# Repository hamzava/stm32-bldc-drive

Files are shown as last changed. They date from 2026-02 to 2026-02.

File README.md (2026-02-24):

# ⚡ Sensorless 3-Phase BLDC Motor Driver  
### Using STM32F411RE + IR2110 Gate Drivers + IRF3205

> 📌 **Recommended Reading:**  
> Please refer to `/Docs/BLDC Project Report.pdf` first for a detailed explanation of the architecture, technical challenges encountered, and lessons learned during development.  
> This repository documents a prototype exploration and does not represent a finalized, fully validated motor drive system.

◆ This project represents an exploration into low-level complementary PWM control, high-side bootstrap driving, and discrete 3-phase inverter design using STM32 advanced timers.

---

## ◆ Project Overview

🟥 This project is a  3-phase BLDC motor driver prototype built using:

 - **STM32F411RE** (Advanced Timer – Complementary PWM)
 - **IR2110 High/Low Side Gate Drivers**
 - IRF3205 N-Channel MOSFET Half-Bridges
 - Bootstrap High-Side Supply Topology

🟥 The objective was to implement manual commutation for a sensorless BLDC motor using complementary PWM outputs from the MCU’s advanced timer (TIM1), with register-level control and control the motor using it's BEMF.

This prototype focused on:

✔ BLDC Motor Control Algorithm
✔ Complementary PWM generation  
✔ Gate driver bootstrap behavior  
✔ Register-level commutation control  
✔ Hardware–firmware synchronization  

---
## ◆ Repository Structure
/Hardware
- ├── KiCad_Project
- ├── Gerbers
- ├── Schematics_PDF
- ├── PCB_Images

/Firmware

/Videos

/Docs
- ├── Datasheets
- ├── Resources_Used > ***All the files used to learn about technologies involved in this project***
- ├── BLDC Project Report.pdf

---

## ◆ Status

Prototype exploration complete.  
Further revision planned with improved instrumentation and driver selection.

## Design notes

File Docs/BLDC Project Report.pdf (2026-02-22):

1. System architecture overview

The architecture of the sensor less control drive was based on 3 main components. MCU, IC driver and MOSFET Half Bridges. The idea was to produce PWM using the MCU advanced timer which came with complementary output. This PWM would be used by the IC driver to produce signal for the gate of the MOSFET. We planned to have 3 Half Bridges, 1 for each Phase hence 3 IC drivers. MOSFETs were carefully chosen by considering their critical parameters, in our case for example, Rds(on), Id, Vgs(th) and Qg.

Ideally, we wanted an IC where we would send a high PWM signal to the input, and IC must output 2 complementary signals. In addition to this, an ideal IC would have been which gave us 3 I/O, one for each phase, in one IC rather than using 3 different ICs. FAN73893 was a good match. But it wasn’t available locally, making it unfeasible financially. IR2110 was a not the ideal choice. STM32F411RE was a good choice because it came with PWM. It also had ADC – DAC which we could have used for monitoring speed, speed regulation & position with DMA by using the motor’s BEMF.

2. Lack of Oscilloscope and Resulting limitations

The lack of an Oscilloscope significantly limited the validation of critical parameters for this system such as dead-time, complementary switching and bootstrap charging behaviour. This resulted in a series of after effects. This meant that we can’t visualise the waveforms which we required. We can’t gauge them being precise. Also, with DMM, the PWM is averaged but as we didn’t have an oscilloscope so subsequently, we couldn’t see if the driver was giving us the required output or was there a shoot through.

3. Manual Commutation Attempt

Initially, I wrote the code manually where I had switch cases. A function would then loop for each switch case. The limitation was that, I had to reset the relevant bits in the register with each commutation. This sort of worked but it wasn’t as smooth as expected. The likely cause was that the bit manipulation was not synchronized with the PWM. This didn’t give us a clean transition. So, I think this was an issue to be noted here which prevented me to create smoothness.

4. Discovery of COMG event & shadow registers

COMG event is an atomic event. This means that we get what we want with the least delay as the configurations are effectively transferred from the preload registers to active registers without any interruption whenever there is an update event. It works with storing values in the preload register first and then firing it into the active register when an update event occurs. But, in my opinion, it requires a higher precision of timer configuration.

5. Full timer reset + pull-down attempts

During experimentation, TIM1 CH1 pins to 5V pins on the development board. Henceforth, it wasn’t possible to continue with the project as STM32F411RE has only 3 PWM channels with complementary outputs and one of them was blown up. For TIM1 CH1 being short, we did first check, if the GPIO, AFR, MODER are set up correctly in the software or not. After that, I went through the timer bits over and over again. We set the GPIO pin to analog, but it still showed a short, it showed near zero resistance on the DMM continuity, which suggested the pin was internally short. But, we still tried to reset the timer using RCC register. Lastly, I did also try pulling it down with a resistor but apparently it didn’t work. Not conclusively, but most likely it was an internal ESD which was blown up.

6. Complementary PWM behaviour inconsistencies.

A lot of these inconsistencies stayed unresolved due to lack of an Oscilloscope. One of the most dangerous observations one can have in such a system, both outputs of the same PWM channel being high at the same time. This is the root cause of a shoot through. Furthermore, sometimes for 50% duty cycle of 3.3V signal, the main channel would should 1.6V on DMM, but the complementary channel would show 2.8V. Two issues exist here. First that the DMM suggested that both channels are high at almost the same time although this couldn’t be conclusively verified due to the lack of oscilloscope. But in software, we did hold a commutation step for enough time which let us retrieve the readings from each channel.

The second is that the complementary channel is not following the set duty cycle. For such cases, we tried manipulating registers precisely with bits such as OCxREF, OSSR, OISx, CCPC, CCUS etc as the PWM outputs are the product of some of these btis. Ideally, the channel should be disabled by CCxNE but many times we still observed an output, despite manipulating bits mentioned earlier, it didn’t change. This was one of the main cases we observed. Rest were pretty similar like a channel won’t show an output when it is supposed to or vice versa. The values wouldn’t match the duty cycle. With Point 2, I would observe switching values as per the commutation sequence but sometimes inconsistencies mentioned above occurred. After COMG implementation, we didn’t get much to observe as the TIM1 CH1 was shorted to 5V on the development board.

7. Bootstrap circuit issues

A common issue I came across with the bootstrap was that the Vs was reflected to HO pin as it is. Ideally it should be Vho=Vs+Vbs. The most likely cause was the Vdd of the driver. I isolated one half bridge and replicated the circuit. It worked as I wanted it and then I replicated it back. One of the most confusing thing was that the bootstrap capacitor was charging but it didn’t discharge. It only discharged, after my DMM probes were across it. This also shows a symptom of the IC driver not working as intended hence we get a reflection of Vs at the HO pin.

8. Importance of Flyback diode and Pull Down Registers

Upon research, there was still more room for additional protection like flyback protection and pull-down resistor at the gate of the MOSFETs. Flyback Protection would protect the MOSFETs from an inductive kickback from the motor. The pull-down resistors at the gate make sure that the gate has a defined state preventing any operation due to possible driver latch-up or any other leakages.

9. Final technical lessons

A better research on component selection and the system architecture could have been done. Projects which involve any sort of medium/high speed switching must only be done if you have an oscilloscope. Instrumentation is critical for such projects. Early access to an oscilloscope would have helped us debug the system much earlier and quicker. A thorough mental and software simulation is always needed before designing hardware. The constraints must be given appropriate time for discussion before the hardware is designed.

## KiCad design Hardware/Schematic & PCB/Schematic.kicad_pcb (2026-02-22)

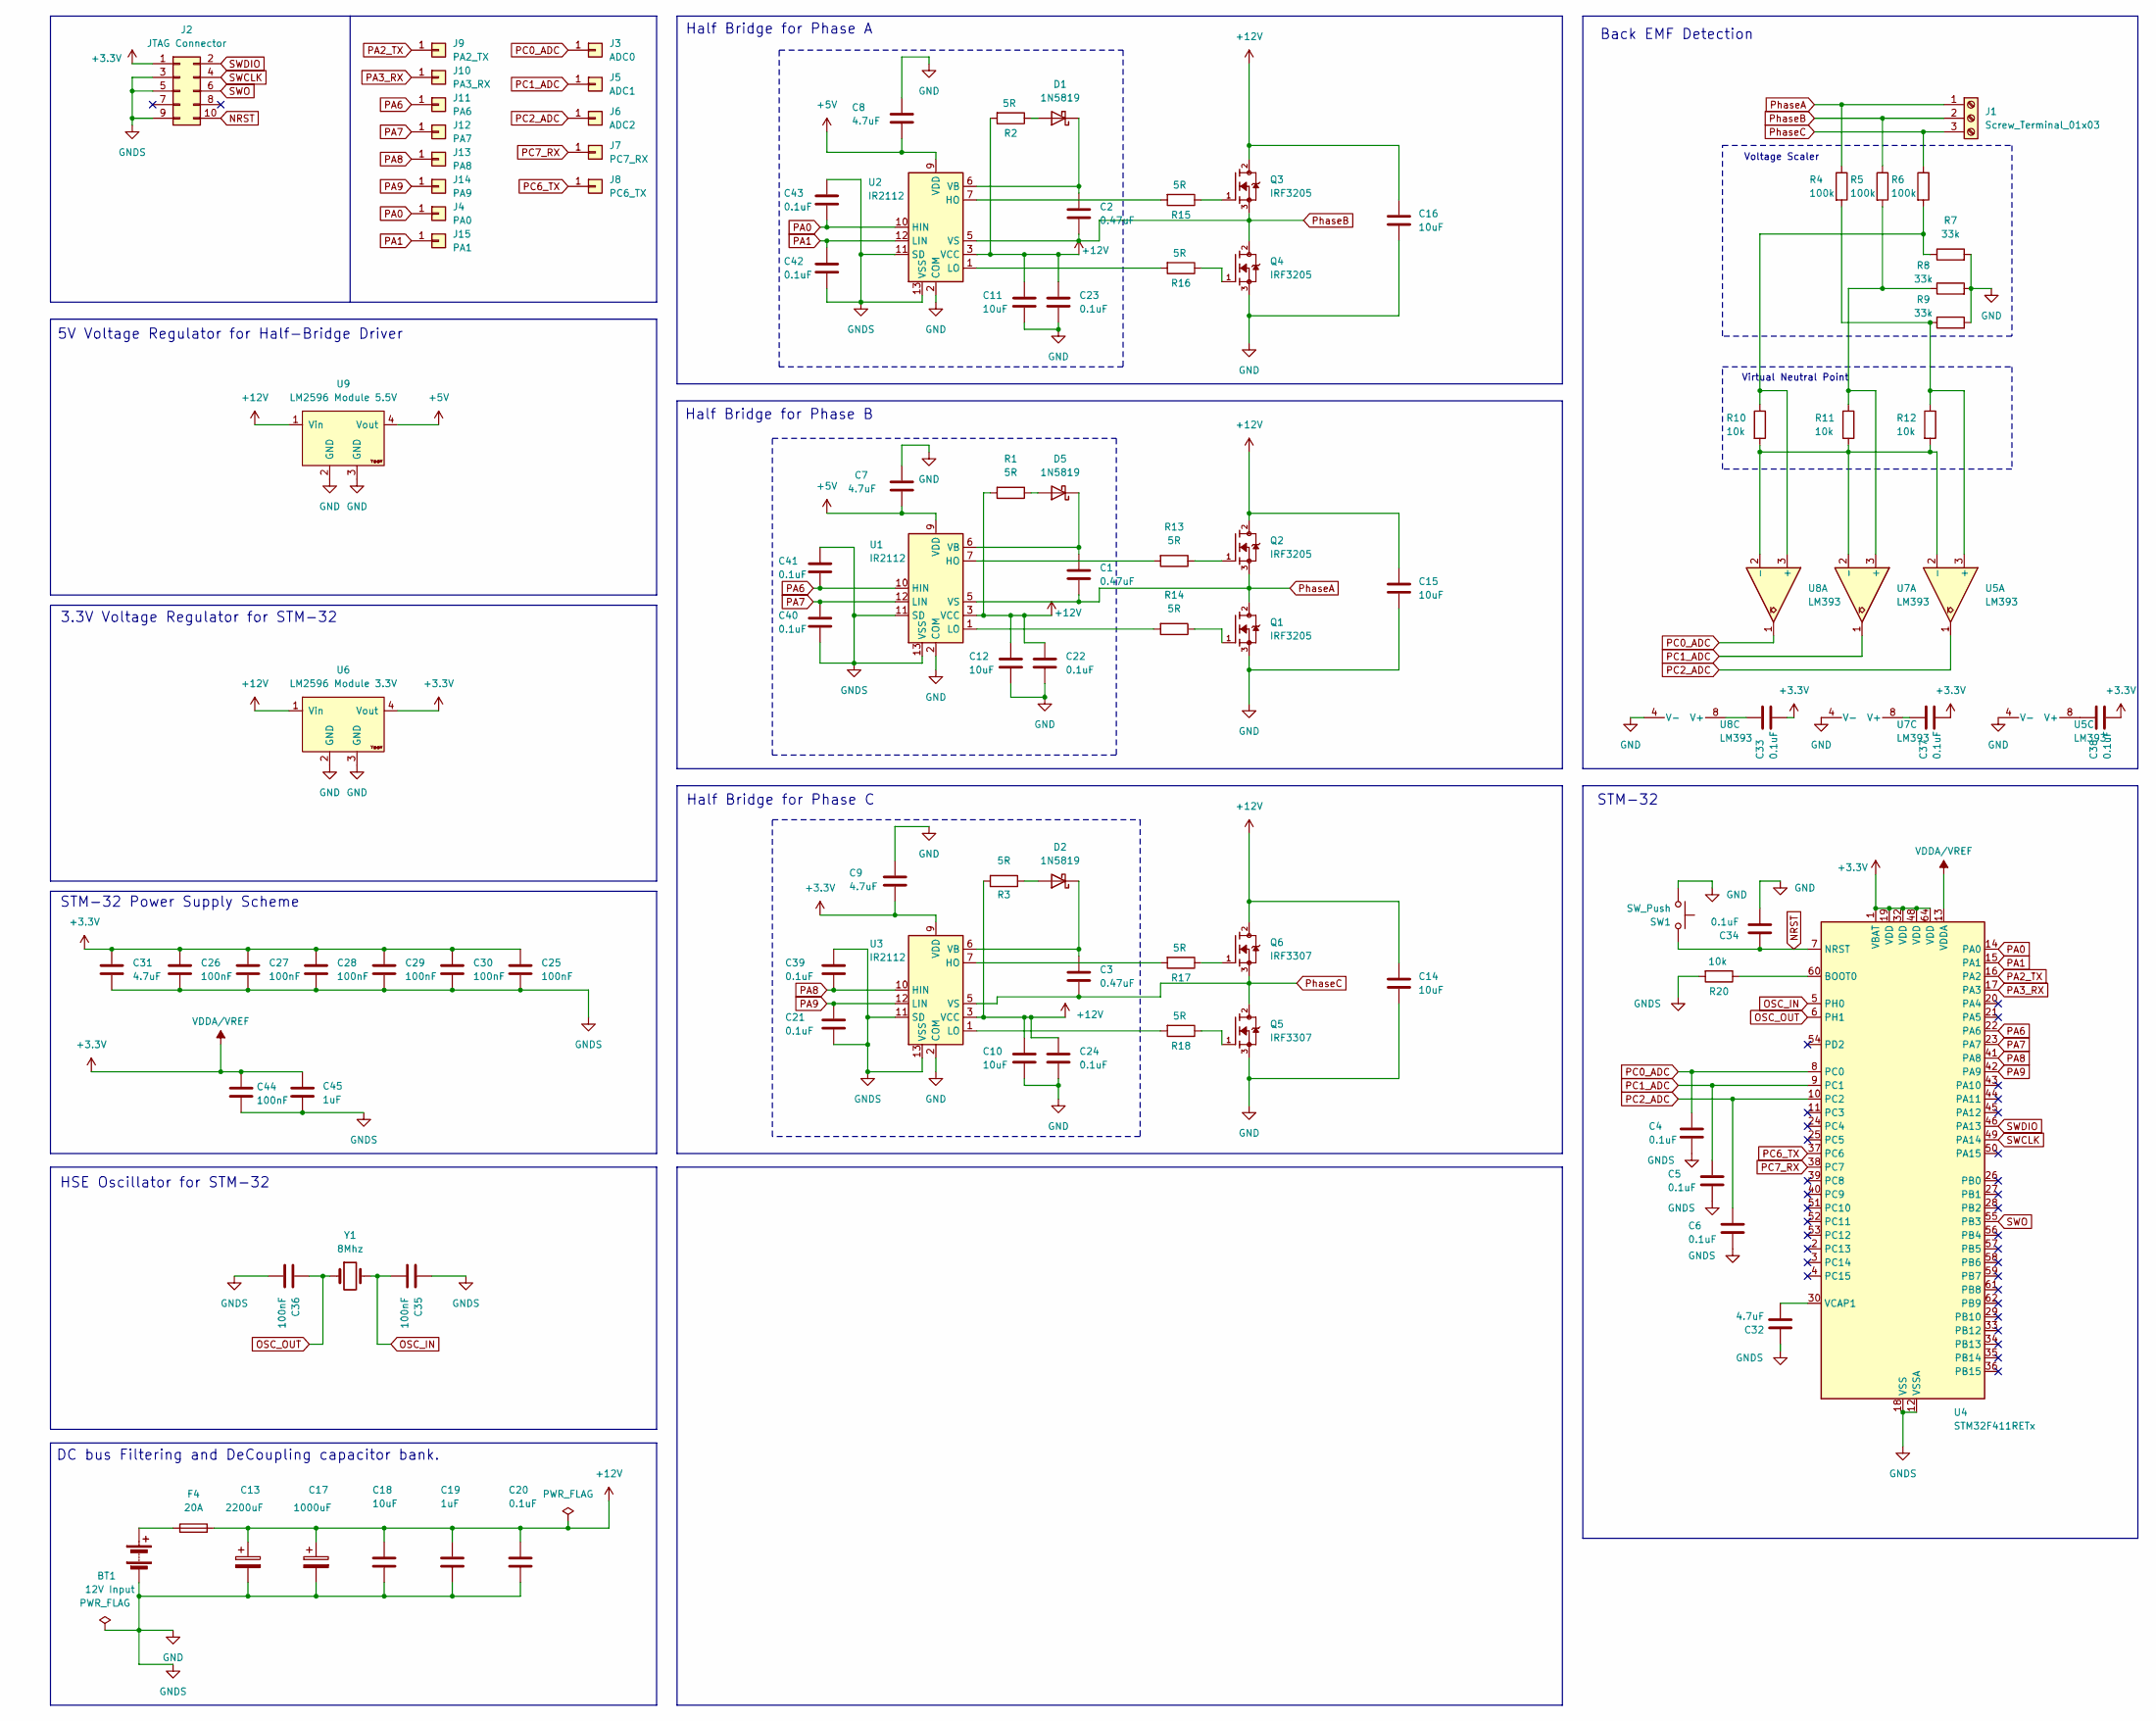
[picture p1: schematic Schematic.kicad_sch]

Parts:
BT1: 12V Input; AMASS_XT60-F_1x02_P7.20mm_Vertical
C1, C2, C3: 0.47uF; C_Disc_D4.3mm_W1.9mm_P5.00mm
C4, C5, C6, C20, C21, C22, C23, C24, C33, C34, C37, C38, C39, C40, C41, C42, C43: 0.1uF; C_Disc_D4.3mm_W1.9mm_P5.00mm
C7, C8, C9, C31, C32: 4.7uF; C_Disc_D4.3mm_W1.9mm_P5.00mm
C10, C11, C12, C14, C15, C16, C18: 10uF; C_Disc_D4.3mm_W1.9mm_P5.00mm
C13: 2200uF; CP_Radial_D10.0mm_P5.00mm
C17: 1000uF; CP_Radial_D8.0mm_P3.50mm
C19, C45: 1uF; C_Disc_D4.3mm_W1.9mm_P5.00mm
C25, C26, C27, C28, C29, C30, C35, C36, C44: 100nF; C_Disc_D4.3mm_W1.9mm_P5.00mm
D1, D2, D5: 1N5819; D_DO-35_SOD27_P7.62mm_Horizontal
F4: 20A; Fuseholder_Clip-5x20mm_Eaton_1A5601-01_Inline_P20.80x6.76mm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
J1: Screw_Terminal_01x03; TerminalBlock_MaiXu_MX126-5.0-03P_1x03_P5.00mm
J2: JTAG Connector; PinHeader_2x05_P2.54mm_Vertical
J3: ADC0; PinHeader_1x01_P1.00mm_Vertical
J4: PA0; PinHeader_1x01_P1.00mm_Vertical
J5: ADC1; PinHeader_1x01_P1.00mm_Vertical
J6: ADC2; PinHeader_1x01_P1.00mm_Vertical
J7: PC7_RX; PinHeader_1x01_P1.00mm_Vertical
J8: PC6_TX; PinHeader_1x01_P1.00mm_Vertical
J9: PA2_TX; PinHeader_1x01_P1.00mm_Vertical
J10: PA3_RX; PinHeader_1x01_P1.00mm_Vertical
J11: PA6; PinHeader_1x01_P1.00mm_Vertical
J12: PA7; PinHeader_1x01_P1.00mm_Vertical
J13: PA8; PinHeader_1x01_P1.00mm_Vertical
J14: PA9; PinHeader_1x01_P1.00mm_Vertical
J15: PA1; PinHeader_1x01_P1.00mm_Vertical
Q1, Q2, Q3, Q4: IRF3205; TO254P1041X444X2933-3; PARTREV 01/25/01
Q5, Q6: IRF3307; TO254P1041X444X2933-3; PARTREV 01/25/01
R1, R2, R3, R13, R14, R15, R16, R17, R18: 5R; R_Axial_DIN0207_L6.3mm_D2.5mm_P7.62mm_Horizontal
R4, R5, R6: 100k; R_Axial_DIN0207_L6.3mm_D2.5mm_P7.62mm_Horizontal
R7, R8, R9: 33k; R_Axial_DIN0207_L6.3mm_D2.5mm_P7.62mm_Horizontal
R10, R11, R12, R20: 10k; R_Axial_DIN0207_L6.3mm_D2.5mm_P7.62mm_Horizontal
SW1: SW_Push; SW_PUSH_6mm
U1, U2, U3: IR2112; DIP-14_W7.62mm
U4: STM32F411RETx; LQFP-64_10x10mm_P0.5mm
U5, U7, U8: LM393; DIP-8_W7.62mm_Socket
U6: LM2596 Module 3.3V; YAAJ_DCDC_StepDown_LM2596
U9: LM2596 Module 5.5V; YAAJ_DCDC_StepDown_LM2596
Y1: 8Mhz; Crystal_HC49-U_Vertical

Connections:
+3.3V: C9.2, C25.1, C26.1, C27.1, C28.1, C29.1, C30.1, C31.1, C33.2, C37.2, C38.2, C44.2, C45.2, J2.1, U3.9 (VDD), U4.1 (VBAT), U4.13 (VDDA), U4.19 (VDD), U4.32 (VDD), U4.48 (VDD), U4.64 (VDD), U6.4 (Vout)
+5V: C7.2, C8.2, U1.9 (VDD), U2.9 (VDD), U9.4 (Vout)
+12V: C10.1, C11.1, C12.1, C13.1, C14.1, C15.1, C16.1, C17.1, C18.1, C19.1, C20.1, C22.1, C23.1, C24.1, F4.2, Q2.2, Q3.2, Q6.2, R1.2, R2.2, R3.2, U1.3 (VCC), U2.3 (VCC), U3.3 (VCC), U6.1 (Vin), U9.1 (Vin)
GND: BT1.2 (-), C4.2, C5.2, C6.2, C7.1, C8.1, C9.1, C10.2, C11.2, C12.2, C13.2, C14.2, C15.2, C16.2, C17.2, C18.2, C19.2, C20.2, C21.2, C22.2, C23.2, C24.2, C25.2, C26.2, C27.2, C28.2, C29.2, C30.2, C31.2, C32.1, C34.2, C35.1, C36.2, C39.1, C40.2, C41.1, C42.2, C43.1, C44.1, C45.1, J2.3, J2.5, J2.9, Q1.3, Q4.3, Q5.3, R7.2, R8.2, R9.2, R20.2, SW1.1, U1.2 (COM), U1.11 (SD), U1.13 (VSS), U2.2 (COM), U2.11 (SD), U2.13 (VSS), U3.2 (COM), U3.11 (SD), U3.13 (VSS), U4.12 (VSSA), U4.18 (VSS), U4.31 (VSS), U4.47 (VSS), U4.63 (VSS), U5.4 (V-), U6.2 (GND), U6.3 (GND), U7.4 (V-), U8.4 (V-), U9.2 (GND), U9.3 (GND)
NRST: C34.1, J2.10, SW1.2, U4.7 (NRST)
unnamed: BT1.1 (+), F4.1
unnamed: D1.2 (A), R2.1
unnamed: C2.1, D1.1 (K), U2.6 (VB)
unnamed: D2.2 (A), R3.1
unnamed: C3.1, D2.1 (K), U3.6 (VB)
unnamed: D5.2 (A), R1.1
unnamed: C1.1, D5.1 (K), U1.6 (VB)
unnamed: Q1.1, R14.1
unnamed: Q2.1, R13.1
unnamed: Q3.1, R15.1
unnamed: Q4.1, R16.1
unnamed: Q5.1, R18.1
unnamed: Q6.1, R17.1
unnamed: R13.2, U1.7 (HO)
unnamed: R14.2, U1.1 (LO)
unnamed: R15.2, U2.7 (HO)
unnamed: R16.2, U2.1 (LO)
unnamed: R17.2, U3.7 (HO)
unnamed: R18.2, U3.1 (LO)
unnamed: R20.1, U4.60 (BOOT0)
unnamed: C32.2, U4.30 (VCAP1)
unnamed: R4.2, R9.1, R12.1, U5.3 (+)
unnamed: R10.2, R11.2, R12.2, U5.2 (-), U7.2 (-), U8.2 (-)
unnamed: C38.1, U5.8 (V+)
unnamed: R5.2, R8.1, R11.1, U7.3 (+)
unnamed: C37.1, U7.8 (V+)
unnamed: R6.2, R7.1, R10.1, U8.3 (+)
unnamed: C33.1, U8.8 (V+)
OSC_IN: C35.2, U4.5 (PH0), Y1.2
OSC_OUT: C36.1, U4.6 (PH1), Y1.1
PA0: C43.2, J4.1, U2.10 (HIN), U4.14 (PA0)
PA1: C42.1, J15.1, U2.12 (LIN), U4.15 (PA1)
PA2_TX: J9.1, U4.16 (PA2)
PA3_RX: J10.1, U4.17 (PA3)
PA6: C41.2, J11.1, U1.10 (HIN), U4.22 (PA6)
PA7: C40.1, J12.1, U1.12 (LIN), U4.23 (PA7)
PA8: C39.2, J13.1, U3.10 (HIN), U4.41 (PA8)
PA9: C21.1, J14.1, U3.12 (LIN), U4.42 (PA9)
PC0_ADC: C4.1, J3.1, U4.8 (PC0), U8.1
PC1_ADC: C5.1, J5.1, U4.9 (PC1), U7.1
PC2_ADC: C6.1, J6.1, U4.10 (PC2), U5.1
PC6_TX: J8.1, U4.37 (PC6)
PC7_RX: J7.1, U4.38 (PC7)
PhaseA: C1.2, J1.1, Q1.2, Q2.3, R4.1, U1.5 (VS)
PhaseB: C2.2, J1.2, Q3.3, Q4.2, R5.1, U2.5 (VS)
PhaseC: C3.2, J1.3, Q5.2, Q6.3, R6.1, U3.5 (VS)
SWCLK: J2.4, U4.49 (PA14)
SWDIO: J2.2, U4.46 (PA13)
SWO: J2.6, U4.55 (PB3)

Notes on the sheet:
HSE Oscillator for STM-32
STM-32 Power Supply Scheme
Virtual Neutral Point
STM-32
Back EMF Detection
Half Bridge for Phase A
DC bus Filtering and DeCoupling capacitor bank.
Voltage Scaler
5V Voltage Regulator for Half-Bridge Driver
Half Bridge for Phase B
Half Bridge for Phase C
3.3V Voltage Regulator for STM-32

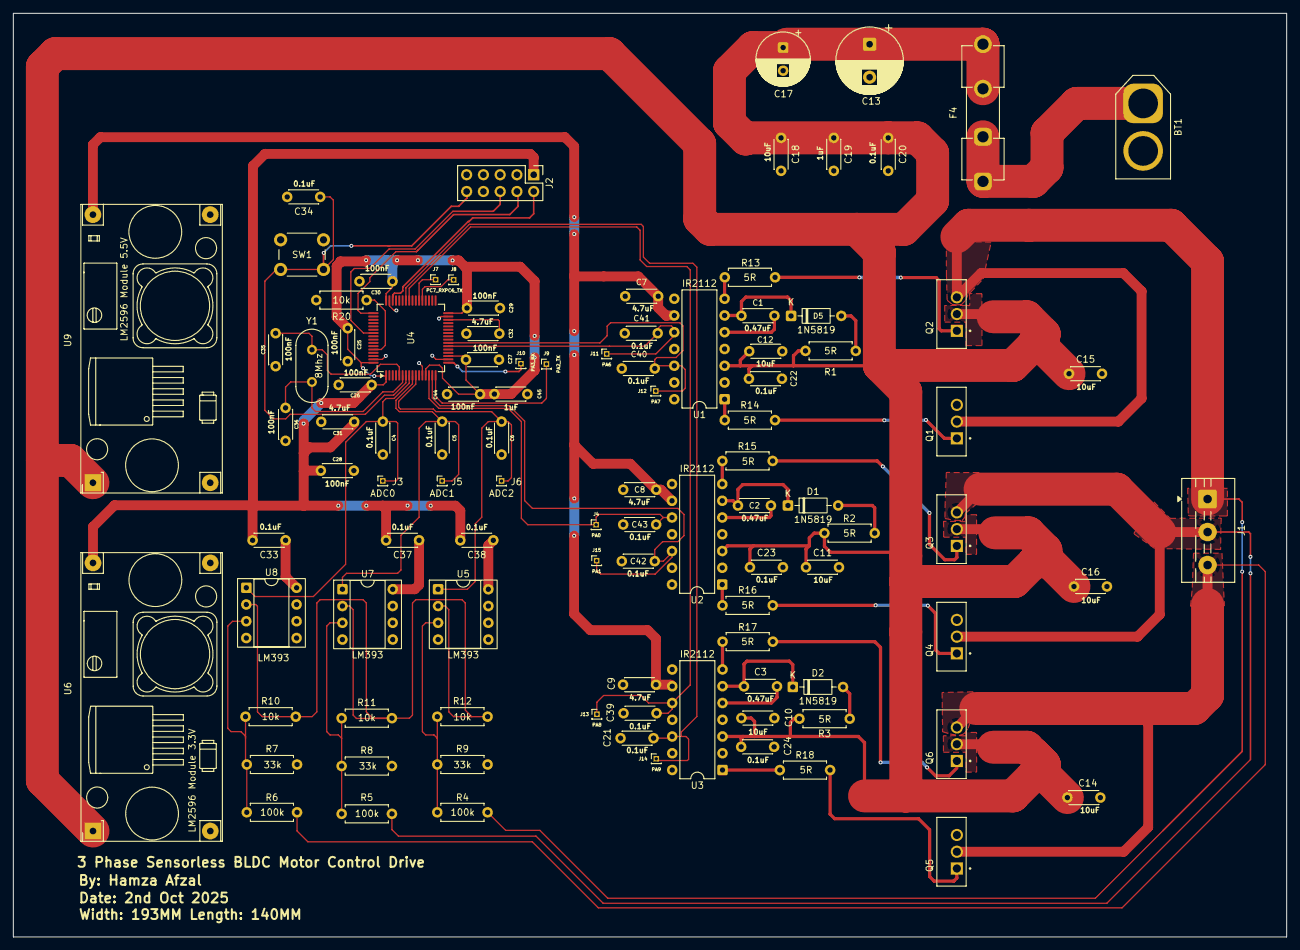
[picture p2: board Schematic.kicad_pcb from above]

Board: 2 copper layers, 193.0 x 140.0 mm, 101 parts (0 on the bottom side), 54 nets.

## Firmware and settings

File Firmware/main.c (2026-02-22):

#include "stm32f4xx.h"
#include <stdint.h>
#include <stdio.h>
#include "main.h"
#include "timer.h"
#include "uart.h"


void MODER(void);
void AFR(void);

int main(void){

	RCC->AHB1ENR |= (0b1111 << 0);	 // Enable GPIOA, GPIOB, GPIOC, GPIOD

    RCC->APB1ENR |= (0b11 << 0);		// Enable TIM2, TIM3
	RCC->APB1ENR |= (1U<<17);

    RCC->APB2ENR |= ((1U << 0) | (1U << 4) );		// Enable TIM1, USART1


    uart2_tx_init();

//    for(uint32_t i =0; i<10; i++){
//        printf("UART Initiated...\n\r");
//    }

    MODER();

    AFR();

    GPIOC->ODR |= (1U<<13);

	TIM2_init();

	TIM1_PWM();



	while(1){

		commutation();

		delay_us(40000000); // for teting purpose i want to see the voltage at all pins

	}

}

void MODER(void){

	GPIOA->MODER |= (1U<<15);		// PA7 set to AFR for TIM1_CH1N MODER7[15:14] OK
	GPIOA->MODER |= (1U<<17); 		// PA8 set to AFR for TIM1_CH1 MODER8[17:16] OK
	GPIOA->MODER |= (1U<<19); 		// PA9 set to AFR for TIM1_CH2 MODER9[19:18] OK
	GPIOA->MODER |= (1U<<21);		// PA10 set to AFR for TIM1_CH3 MODER10 [21:20] OK

	GPIOB->MODER |= (1U<<1); 		// PB0 set to AFR for TIM1_CH2N MODER0[0:1] OK
	GPIOB->MODER |= (1U<<3);		// PB1 set to AFR for TIM1_CH3N MODER1[3:2] OK


	/* 3. Set PC13 as Output */
	GPIOC->MODER |= (1U<<26); // Bit 26 - Set to 1
	GPIOC->MODER &=~ (1U<<27); // Bit 27 - Set to 0

//	GPIOC->MODER |= (1U<<13); 		// PC6 set to AFR for TIM3_CH1 MODER7[13:12] OK
//	GPIOC->MODER |= (1U<<15);		// PC7 set to AFR for TIM3_CH2 MODER7[15:14] OK
//	GPIOC->MODER |= (1U<<17); 		// PC8 set to AFR for TIM3_CH3 MODER8[17:16] OK
//
//	//PC13, PC14, PC15 as Input
//	GPIOC->MODER &=~ (0b11<<26); 	//PC13 MODER13	[27:26] OK
//	GPIOC->MODER &=~ (0b11<<28); 	//PC14 MODER14 [29:28] OK
//	GPIOC->MODER &=~ (0b11<<30); 	//PC15 MODER15 [31:30] OK

	GPIOA->PUPDR = 0;

	GPIOA->PUPDR |= (1U<<15);
	GPIOA->PUPDR |= (1U<<17);
	GPIOA->PUPDR |= (1U<<19);
	GPIOA->PUPDR |= (1U<<21);

	GPIOB->PUPDR |= (1U<<1);
	GPIOB->PUPDR |= (1U<<3);


}
void AFR(void){

	GPIOA->AFR[0] |= (1U<<28); 		// PA7 TIM1_CH1N AF01 AFRL7[31:28] OK
	GPIOA->AFR[1] |= (1U<<0); 		// PA8 TIM1_CH1 AF01 AFRH8[3:0] OK
	GPIOA->AFR[1] |= (1U<<4); 		// PA9 TIM1_CH2 AF01 AFRH9[7:4] OK
	GPIOA->AFR[1] |= (1U<<8); 		// PA10 TIM1_CH3 AF01 AFRH10[11:8] OK

	GPIOB->AFR[0] |= (1U<<0); 		// PB0 TIM1_CH2N AF01 AFRL0[3:0] OK
	GPIOB->AFR[0] |= (1U<<4); 		// PB1 TIM1_CH3N AF01 AFRL1[7:4] OK
//
//	GPIOC->AFR[0] |= (1U<<25); 		// PC6 TIM3_CH1 AF02 AFRL6[27:24] OK
//	GPIOC->AFR[0] |= (1U<<29); 		// PC7 TIM3_CH2 AF02 AFRL[31:28] OK
//	GPIOC->AFR[1] |= (1U<<1); 		// PC8 TIM3_CH3 AF02 AFRH8[3:0] OK

}

void led_toggle(void)
{
	GPIOC->ODR ^= (1U<<13); // Bit 5 - Toggle PA5
}

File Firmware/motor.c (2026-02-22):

#include "stm32f4xx.h"
#include <stdint.h>
#include <stdio.h>
#include "main.h"
#include "timer.h"

#define Phase_A_High	(TIM_CCER_CC1E)
#define Phase_A_Low		(TIM_CCER_CC1NE)
#define Phase_B_High	(TIM_CCER_CC2E)
#define Phase_B_Low		(TIM_CCER_CC2NE)
#define Phase_C_High	(TIM_CCER_CC3E)
#define Phase_C_Low		(TIM_CCER_CC3NE)

#define PWM_MODE		(0b110)
#define FORCE_INACTIVE	(0b100)
#define	FORCE_ACTIVE	(0b101)

#define CCMR1_OC1M		(0b111<<4)
#define CCMR1_OC2M		(0b111<<12)
#define CCMR2_OC3M		(0b111<<4)

#define CCER_ENABLE_MASK 		(Phase_A_High | Phase_A_Low | Phase_B_High | Phase_B_Low | Phase_C_High | Phase_C_Low)

#define CCMR1_ENABLE_MASK	(CCMR1_OC1M | CCMR1_OC2M)
#define CCMR2_ENABLE_MASK	(CCMR2_OC3M)

static uint8_t step = 0;

static Step_Configuration config_table[6] = {

		// 0. A+, B- // A8, B0
		{
				.ccer	= (Phase_A_High | Phase_B_Low),
				.ccmr1 	= ((PWM_MODE<<TIM_CCMR1_OC1M_Pos) |(FORCE_ACTIVE<<TIM_CCMR1_OC2M_Pos)),
				.ccmr2	= (FORCE_INACTIVE<<TIM_CCMR2_OC3M_Pos),
				// Phase A 100 -> 110, Phase B 100 -> 101, Phase C 100->100
				//.ccr 	= {200,200,0},
		},

		// 1. A+, C- //  A8, B1
		{
				.ccer	= Phase_A_High | Phase_C_Low,
				.ccmr1 	= ((PWM_MODE<<TIM_CCMR1_OC1M_Pos) |(FORCE_INACTIVE<<TIM_CCMR1_OC2M_Pos) ),
				.ccmr2	= (FORCE_ACTIVE<<TIM_CCMR2_OC3M_Pos),
				// Phase A 110 -> 110, Phase B 101 -> 100, Phase C 100->101
				//.ccr 	= {200,0,200},

		},
		// 2. B+, C- // A9, B1
		{
				.ccer	= Phase_B_High | Phase_C_Low,
				.ccmr1 	= ((FORCE_INACTIVE<<TIM_CCMR1_OC1M_Pos) |(PWM_MODE<<TIM_CCMR1_OC2M_Pos )),
				.ccmr2	= (FORCE_ACTIVE<<TIM_CCMR2_OC3M_Pos),
				// Phase A 110 -> 100, Phase B 100 -> 110, Phase C 101->101
				//.ccr 	= {0,200,200},

		},
		// 3. B+, A- // A9, A7
		{
				.ccer	= Phase_B_High | Phase_A_Low,
				.ccmr1 	= ((FORCE_ACTIVE<<TIM_CCMR1_OC1M_Pos) |(PWM_MODE<<TIM_CCMR1_OC2M_Pos )),
				.ccmr2	= (FORCE_INACTIVE<<TIM_CCMR2_OC3M_Pos),
				// Phase A 100 -> 101, Phase B 110 -> 110, Phase C 101->100
				//.ccr 	= {200,200,0},

		},
		// 4. C+, A- // A10, A7
		{
				.ccer	= Phase_C_High | Phase_A_Low,
				.ccmr1 	= ((FORCE_ACTIVE<<TIM_CCMR1_OC1M_Pos)|(FORCE_INACTIVE<<TIM_CCMR1_OC2M_Pos) ),
				.ccmr2	= (PWM_MODE<<TIM_CCMR2_OC3M_Pos),
				// Phase A 101 -> 101, Phase B 110 -> 100, Phase C 100->110
				//.ccr 	= {200,0,200},

		},
		// 5. C+, B- // A10, B0
		{
				.ccer	= Phase_C_High | Phase_B_Low,
				.ccmr1 	= ((FORCE_INACTIVE<<TIM_CCMR1_OC1M_Pos )|(FORCE_ACTIVE<<TIM_CCMR1_OC2M_Pos )),
				.ccmr2	= (PWM_MODE<<TIM_CCMR2_OC3M_Pos),
				// Phase A 101 -> 100, Phase B 100 -> 101, Phase C 110->110
				//.ccr 	= {0,200,200},

		},

};



void commutation(void){

	//Step_Configuration* config = &config_table[step];
	TIM1->CCMR1 &=~ CCMR1_ENABLE_MASK;
	TIM1->CCMR1 |= config_table[step].ccmr1;

	TIM1->CCMR2 &=~ CCMR2_ENABLE_MASK;
	TIM1->CCMR2 |= config_table[step].ccmr2;

	TIM1->CCER &=~ CCER_ENABLE_MASK;
	TIM1->CCER |= config_table[step].ccer;


//	TIM1->CCR1	= config->ccr[0];
//	TIM1->CCR2	= config->ccr[1];
//	TIM1->CCR3	= config->ccr[2];

	TIM1->EGR = TIM_EGR_COMG;

	delay_us(10);

	step++;

    if(step >= 6){ // this is for testing only

    	step = 4;

    }


}

void set_duty_cycle(uint16_t duty){

	TIM1->CCR1 = duty;
	TIM1->CCR2 = duty;
	TIM1->CCR3 = duty;

}

void delay_us(uint32_t us){

    TIM2->CNT = 0;           // reset the counter

   // led_toggle();

    while (TIM2->CNT < us);  // wait until desired count

}

void ramp(void){


	TIM1->CCR1 = 100;
	TIM1->CCR2 = 100;
	TIM1->CCR3 = 100;

	uint16_t delay = 3000;

	uint8_t lap = 0;

	//TIM4-> CNT = 0;

	while(delay >100 && TIM1->CCR1 < 600) {

		if(lap<=5){

			for(uint8_t step = 1; step <= 6; step++){
						printf("Step %d\r\n", step);
						//commutation(step);
						delay_us(delay);
				}

			if(delay!=100){
				delay = delay - 100;
			}

			lap ++;
		}

		if(TIM1->CCR1!=600){
			TIM1->CCR1 = TIM1->CCR1 + 100;
			TIM1->CCR2 = TIM1->CCR2 + 100;
			TIM1->CCR3 = TIM1->CCR3 + 100;
		}

	}

}

void alignment(void){

	printf("Starting Alignment\r\n");

	//commutation(10);

//	for(uint8_t step = 1; step<=1; step++){
//
//		printf("Aligning for Step: %d\r\n", step);
//
//		commutation(step);
//
//		delay_us(1000000); // 1 Second Delay
//	}

	printf("Alignment Over\r\n");

}

void commutation_old(uint8_t step){

    TIM1->CCER &= ~(
        Phase_A_High | Phase_A_Low |
        Phase_B_High | Phase_B_Low |
        Phase_C_High | Phase_C_Low
    );

	switch(step){
	case 1:
		// 60 Degree - Phase C floats - Falling Edge BEMF Zero Crossing
		printf("60 Degree...\r\n");
		TIM1->CCER = Phase_A_High | Phase_B_Low;
		//TIM1->CCER = Phase_B_Low;

		break;

	case 2:
		// 120 Degree - Phase B floats - Rising Edge BEMF Zero Crossing
		printf("120 Degree...\r\n");
		TIM1->CCER = Phase_A_High | Phase_C_Low;
		//TIM1->CCER = Phase_C_Low;

		break;
	case 3:
		// 180 Degree - Phase A floats - Falling Edge BEMF Zero Crossing
		printf("180 Degree...\r\n");
		TIM1->CCER = Phase_B_High | Phase_C_Low;
		//TIM1->CCER = Phase_C_Low;
		break;

	case 4:
		// 240 Degree - Phase C floats - Rising Edge BEMF Zero Crossing
		printf("240 Degree...\r\n");
		TIM1->CCER = Phase_B_High | Phase_A_Low;
		//TIM1->CCER = Phase_A_Low;

		break;
	case 5:
		// 300 Degree - Phase B floats - Falling Edge BEMF Zero Crossing
		printf("300 Degree...\r\n");
		TIM1->CCER = Phase_C_High | Phase_A_Low;
		//TIM1->CCER = Phase_A_Low;

		break;
	case 6:
		// 360 Degree - Phase A floats - Rising Edge BEMF Zero Crossing
		printf("360 Degree...\r\n");
		TIM1->CCER = Phase_C_High | Phase_B_Low;
		//TIM1->CCER = Phase_B_Low;
		break;
	case 7:
		//TIM1->CCER = Phase_A_Low | Phase_B_Low | Phase_C_Low ;
		printf("Step 7... Phase_A_High | Phase_B_Low\r\n");
		TIM1->CCER = Phase_A_High | Phase_B_Low;
		break;
	case 8:
		//TIM1->CCER = Phase_A_Low | Phase_B_Low | Phase_C_Low ;
		printf("Step 8... Phase_B_High | Phase_C_Low \r\n");
		TIM1->CCER = Phase_B_High | Phase_C_Low;
		break;
	case 9:
		//TIM1->CCER = Phase_A_Low | Phase_B_Low | Phase_C_Low ;
		printf("Step 9... Phase_C_High | Phase_B_Low \r\n");
		TIM1->CCER = Phase_C_High | Phase_B_Low;
		break;
	case 10:
		printf("Alignment Phase A \r\n");
		TIM1->CCR1 = 200;
		TIM1->CCER |= Phase_A_High | Phase_A_Low;

		//delay(1000000);

		TIM1->CCER &=~ Phase_A_High | Phase_A_Low;
		TIM1->CCR1=400;
	}

}
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
